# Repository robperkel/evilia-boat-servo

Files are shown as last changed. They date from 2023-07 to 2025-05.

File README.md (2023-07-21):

# Dr. Evilia's Boat Sampling HAT
This custom HAT is used to better implement control of the servos and motors used on her sampling boat. We found there wasn't a good "off-the-shelf" board available that fit the desired specifications. This project is designed around a small, 8-bit microcontroller that provides a far more intelligent and flexible design interface. 

This repository contains the documentation, hardware files, and firmware used for this project. The boat runs on a Raspberry Pi 4, Model B.  

## Table of Contents

- [Base Software](#base-software)
- [Tools Needed](#tools-needed)
    - [Other Tools Used](#other-tools-used)
- [Bill of Materials (BOM)](#bill-of-materials-bom)
- [Design Objectives](#design-objectives)
- [Microcontroller Pinout](#microcontroller-pinout)
- [Software Registers](#software-registers)
- [Digital Control](#digital-control)
- [Analog Control](#analog-control)
- [Usage from Raspberry Pi](#usage-from-raspberry-pi)

## Base Software

This bare metal I<sup>2</sup>C driver was used as a code base: https://github.com/microchip-pic-avr-examples/pic18f56q71-bare-metal-i2c-mplab 

**Per the license agreement in this code, the firmware (specifically the I<sup>2</sup>C driver) can ONLY be used with Microchip microcontrollers.** This is not an issue as the physical board is not compatiable with other microcontrollers.

## Tools Needed

- Programming / Development IDE: [MPLAB&reg; X IDE v6.10](https://www.microchip.com/en-us/tools-resources/develop/mplab-x-ide)
- Compiler: [MPLAB XC8 v2.41](https://www.microchip.com/en-us/tools-resources/develop/mplab-xc-compilers/downloads-documentation#XC8)  
- Programmer: [MPLAB SNAP](https://www.microchip.com/en-us/development-tool/PG164100) or [PICKIT&trade; 4](https://www.microchip.com/en-us/development-tool/PG164140)

### Other Tools Used

- I<sup>2</sup>C Tester (for development): [MCP2221A Breakout Module (ADM00559)](https://www.microchip.com/en-us/development-tool/ADM00559)
- Block Diagrams: [Draw.io](https://app.diagrams.net/)
- Schematic and PCB Generation: [KiCad 7](https://www.kicad.org/)
- PCB Vendor: [OSH Park](https://oshpark.com/)
    - If ordering from a different vendor, I recommend choosing a surface finish such as ENIG to provide some corrosion resistance in the high humidity environment.
    - Conformally coating the board is also recommended.

## Bill of Materials (BOM)

Order PCBs directly from the [OSH Park Project Page](https://oshpark.com/shared_projects/IClJSFr6)  
Digikey Shopping List: [https://www.digikey.com/en/mylists/list/YOLHZE0EBO](https://www.digikey.com/en/mylists/list/YOLHZE0EBO)   
- See [Control Board.xlsx](./Control%20Board/Control%20Board.xlsx) for the BOM
    - Red, struck-through items are not in the BOM
- Includes 0 ohm jumpers for I<sup>2</sup>C Address Setting
- Motor drive parts for `EXT_LED1` are not included
- Optional off-board connectors are not in the list

**Important: Shopping list does NOT include a programmer. Programmers can obtained from Digikey (or other electronics vendor).**

## Design Objectives

1. Support 6x 3-pin servo motors
2. ON/OFF control of a large pump
3. LED outputs for various indicators
4. I<sup>2</sup>C Interface
5. 3.3V logic interface with Raspberry Pi
6. 5V, 500mA motor control (ON/OFF)
7. 50 Hz Servo Frequency

## Microcontroller Pinout

Microcontroller: PIC18F1xQ41
(PIC18F14Q41 / PIC18F15Q41 / PIC18F16Q41)

| Function | Pin (PORT / PIN)
| --- | ---
| VDD (5V) | 1
| VSS (GND) | 20
| nMCLR | 4
| SDA | 2 (RA5)
| SCL | 3 (RA4)
| ADDR0 | 16 (RC0)
| ADDR1 | 13 (RB4)
| Servo 6 | 10 (RB7)
| Servo 5 | 9 (RC7)
| Servo 4 | 8 (RC6)
| Servo 3 | 7 (RC3)
| Servo 2 | 6 (RC4)
| Servo 1 | 5 (RC5)
| EXT_LED | 11 (RB6)
| PUMP_EN | 15 (RC1)
| AN1 | 17 (RA2)
| AN2 | 12 (RB5)
| DEBUG 0 | 19 (RA0 / ICSPDAT)
| DEBUG 1 | 18 (RA1 / ICSPCLK)
| OPAMP_OUT (reserved) | 14 (RC2)

### Notes
1. nMCLR is not available as an I/O in this configuration.
2. DEBUG 0/1 are LED outputs on the board. Unavailable during debugging.
3. EXT_LED can be converted to a 2nd motor/pump enable.
4. OPAMP_OUT is reserved due to internal OPAMP peripheral requirements.  

## Software Registers

**Please see [Registers.md](./Registers.md) for more information**

## Digital Control

### I<sup>2</sup>C Parameters

- Frequency: 100 kHz  
- 7-bit Address: TBD

### I<sup>2</sup>C Communication

### Writing To

The "register address" (Reg. ADDR) selects which setting to change. After this, each data byte is loaded into the next sequential register. 

(Start) &rarr; I<sup>2</sup>C ADDR (W) &rarr; Reg. ADDR &rarr; Data 0 &rarr; Data 1 &rarr; ... &rarr; Data N &rarr; (Stop)

### Reading From

To read from the device, address the microcontroller (write) and send the starting register address. Then, restart communication and address the microcontroller (read). Each byte is read in order from the registers.

(Start) &rarr; I<sup>2</sup>C ADDR (W) &rarr; Reg. ADDR &rarr; (Restart) &rarr; I<sup>2</sup>C ADDR (R) &rarr; Data 0 &rarr; Data 1 &rarr; ... &rarr; Data N &rarr; (Stop)

### Power on Restart (PoR) Behavior

On PoR, the microcontroller sets all duty cycles to 0%, PWM frequencies to 50 Hz, and turns off the LEDs and motor. 

## Analog Control

## Usage from Raspberry Pi

To ease integration in the system, a custom Python library was developed to simplify setup.

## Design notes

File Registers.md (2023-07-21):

# Software Registers

This file contains the software-defined registers, bitfields and allowed values.

## Register Map

| Address | Register Name | Description
| --- | --- | ---
| 0x00 | [STATUS](#status-register-mapping) | Status of the microcontroller
| 0x01 | [OUTPUT](#output-register-mapping) | Sets the output register (overwrites current value)
| 0x02 | [SAMPLE](#sample-register) | Selects the input to sample 
| 0x04 | [ADCH](#adchadcl-register) | ADC Measurement, High Byte
| 0x05 | [ADCL](#adchadcl-register) | ADC Measurement, Low Byte
| 0x06 | [PUMP_TIME](#pump_time-register) | Sets the on time of the PUMP_EN
| 0x07 | [LED_TIME](#led_time-register)  | Sets the on time of the EXT_LED
| 0x0A | [RESET](#reset-register) | Resets the microcontroller and returns  all settings to defaults
| 0x10 | [DC1H](#dcxhdcxl-registers) | Duty Cycle of PWM1, High Byte
| 0x11 | [DC1L](#dcxhdcxl-registers) | Duty Cycle of PWM1, Low Byte
| 0x12 | [DC2H](#dcxhdcxl-registers) | Duty Cycle of PWM2, High Byte
| 0x13 | [DC2L](#dcxhdcxl-registers) | Duty Cycle of PWM2, Low Byte
| 0x14 | [DC3H](#dcxhdcxl-registers) | Duty Cycle of PWM3, High Byte
| 0x15 | [DC3L](#dcxhdcxl-registers) | Duty Cycle of PWM3, Low Byte
| 0x16 | [DC4H](#dcxhdcxl-registers) | Duty Cycle of PWM4, High Byte
| 0x17 | [DC4L](#dcxhdcxl-registers) | Duty Cycle of PWM4, Low Byte
| 0x18 | [DC5H](#dcxhdcxl-registers) | Duty Cycle of PWM5, High Byte
| 0x19 | [DC5L](#dcxhdcxl-registers) | Duty Cycle of PWM5, Low Byte
| 0x1A | [DC6H](#dcxhdcxl-registers) | Duty Cycle of PWM6, High Byte
| 0x1B | [DC6L](#dcxhdcxl-registers) | Duty Cycle of PWM6, Low Byte
| 0x20 | [FRQ1H](#frqxhfrqxl-registers) | Frequency of PWM1/2, High Byte
| 0x21 | [FRQ1L](#frqxhfrqxl-registers) | Frequency of PWM1/2, Low Byte
| 0x22 | [FRQ2H](#frqxhfrqxl-registers) | Frequency of PWM3/4, High Byte
| 0x23 | [FRQ2L](#frqxhfrqxl-registers) | Frequency of PWM3/4, Low Byte
| 0x24 | [FRQ3H](#frqxhfrqxl-registers) | Frequency of PWM5/6, High Byte
| 0x25 | [FRQ3L](#frqxhfrqxl-registers) | Frequency of PWM5/6, Low Byte
| 0x30 | [Analog Configure](#analog-configure-register) | Configures the ADC for Analog Input 1
| 0x31 | [Gain Configure](#gain-configure-register) | Sets the OPAMP gain for Analog Input 1
| 0x32 | [DAC2 Output](#dac2-output-register)
| 0x50 | Firmware Update | Begins a firmware update operation
| 0x51 | Firmware Unlock 1 | See note 6
| 0x52 | Firmware Unlock 2 | See note 6
| 0x60 | Firmware Version ID | Firmware version identifier

### Notes

1. Each PWM is used to control each servo. 
2. PWM frequency and duty cycle is only updated on the low byte.
3. See "OUTPUT Register Mapping" for bitmapping of this byte.
4. Certain registers are kept at different offsets to reduce the chance of accidently modifying these values. 
5. PWM frequency is shared between paired outputs.
6. `Firmware Unlock 1` and `Firmware Unlock 2` are only accessible from a sequential write on `Firmware Update`. Other access attempts will be rejected.

**Note: Firmware update and version ID are currently not implemented.**

### STATUS Register Mapping

| Bit Position(s) | Function 
| --- | ---
| 7 | Pump State
| 6:3 | X
| 2 | EXT_LED State
| 1 | Error
| 0 | Sample Ready

### Notes
1. Sample Ready is cleared automatically when any part of the ADC value is read.  
2. The Error bit is set when an illegal command or operation occurs; Automatically cleared on read.
3. Pump/EXT_LED/PUMP_EN are clones of the `OUTPUT` register values.

### OUTPUT Register Mapping

| Bit Position(s) | Function 
| --- | ---
| 7 | Pump
| 6:3 | X
| 2 | External LED
| 1 | Debug LED1
| 0 | Debug LED0

Note: "X" values are reserved.

### SAMPLE Register

| Value | Sampled Input 
| ----- | ---
| 0x00  | *Unused*
| 0x01  | Analog Input 1
| 0x02  | Analog Input 2
| 0x03  | VSS (Ground)
| 0x04  | DAC2

### ADCH/ADCL Register

This value (up-to 16-bits) is the last conversion result from the ADC. Natively, the ADC is 12 bits. But, oversampling can be used for more resolution.

The ADCH value is the high byte, while the ADCL value is the low byte.

### PUMP_TIME Register

| Bit Position(s) | Function 
| --- | ---
| 7:0 | Maximum time (in seconds) for the pump to be on for

* If `PUMP_TIME` is set to 0, then there is no timeout for the pump. 
* Initializes to 120s on Power on Reset (PoR).

### LED_TIME Register

| Bit Position(s) | Function 
| --- | ---
| 7:0 | Maximum time (in seconds) for the external LED to be on for

* If `LED_TIME` is set to 0, then there is no timeout for the LED. 
* Initializes to 0 (disabled) on Power on Reset (PoR).  

### RESET Register

| Value | Function 
| ----- | ---
| 0x5A  | RESET the microcontroller

Note: All other values loaded into this register are ignored.

### DCxH/DCxL Registers

This register holds the 16-bit value used by the PWM hardware to set the duty cycle. The DCxH value is the high byte, while the DCxL value is the low byte.

### FRQxH/FRQxL Registers

This register holds the 16-bit value used by the PWM hardware to set the period (frequency) of the waveform. The FRQxH value is the high byte, while the FRQxL value is the low byte.

### Analog Configure Register

| Bit Position | Function 
| --- | ---
| 7:6 | Voltage Reference Select
| 5:4 | X
| 3:0 | Averaging Configuration

#### Bit Description

Voltage Reference Select
- 0b00 = VDD (5V)
- 0b01 = FVR 1.024V
- 0b10 = FVR 2.048V
- 0b11 = FVR 4.096V

FVR - Fixed Voltage Reference; Internal to the microcontroller. See datasheet for performance, accuracy, etc...

Averaging Configuration
- 0b0000 = 1 Sample (No Averaging)
- 0b0001 = 2 Samples
- 0b0010 = 4 Samples
- 0b0011 = 8 Samples
- 0b0100 = 16 Samples

Note: Undefined values will be treated as 0b0000 (1 sample).

### Gain Configure Register

| Bit Position | Function 
| --- | ---
| 7:3 | X
| 3:0 | Gain Configuration

Note: "X" values are reserved.

#### Bit Description

Gain Configuration
- 0b1xxx = 1 (Unity Gain)
- 0b0000 = 16/15
- 0b0001 = 8/7
- 0b0010 = 4/3
- 0b0011 = 2
- 0b0100 = 8/3
- 0b0101 = 4
- 0b0110 = 8
- 0b0111 = 16

For gain changes, some time is required for the output to stabilize. But, I<sup>2</sup>C is relatively slow, so there shouldn't be any timing issues with starting a conversion immediately following a gain change (assuming 100 kHz speed). 

### DAC2 Output Register

Sets the output voltage of DAC2. DAC2 uses the 1.024V FVR. The output is set by the formula: Vout = DATA/2^8 * 1.024V

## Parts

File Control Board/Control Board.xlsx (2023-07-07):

Date: | 2023-07-05 12:13
Tool: | Eeschema 7.0.5
Generator: | C:\Program Files\KiCad\7.0\bin\scripting\plugins/bom_csv_grouped_by_value_with_fp.py
Component Count: | 72
Ref | Qnty | Value | Cmp name | Footprint | Description | Vendor | DNP
ADDR0, ADDR1 | 2 | 0 | R_US | Resistor_SMD:R_0805_2012Metric_Pad1.20x1.40mm_HandSolder | Resistor, US symbol |  | DNP
~~ANALOG_EXT1, ANALOG_EXT2~~ | ~~2~~ | ~~Conn_01x03_Pin~~ | ~~Conn_01x03_Pin~~ | ~~Connector_PinHeader_2.54mm:PinHeader_1x03_P2.54mm_Vertical~~ | ~~Generic connector, single row, 01x03, script generated~~ |  | DNP
BAT_IN1 | 1 | BCH-381H-2GN | Terminal_Block_2 | Control Board Custom:BCH-381H-2GN | Terminal Block
~~C1, C3, C5, C7, C8, C9, C10, C11, C12, C13, C14~~ | ~~11~~ | ~~0.01uF~~ | ~~C_Small~~ | ~~Capacitor_SMD:C_0805_2012Metric_Pad1.18x1.45mm_HandSolder~~ | ~~Unpolarized capacitor, small symbol~~ |  | ~~DNP~~
C15 | 1 | 220uF | C_Polarized | Capacitor_THT:C_Radial_D8.0mm_H11.5mm_P3.50mm | Polarized capacitor
C2, C4, C6 | 3 | 0.1uF | C_Small | Capacitor_SMD:C_0805_2012Metric_Pad1.18x1.45mm_HandSolder | Unpolarized capacitor, small symbol
D1 | 1 | MBR0580S1 | MBR0580S1_1 | StandardPackages_Custom:SOD-123 | 0.5A, SMD Schottky Diode
~~D2~~ | ~~1~~ | ~~MBR0580S1~~ | ~~MBR0580S1_1~~ | ~~StandardPackages_Custom:SOD-123~~ | ~~0.5A, SMD Schottky Diode~~ |  | ~~DNP~~
D3, D4 | 2 | SMAJ6.0A | SMAJ | StandardPackages_Custom:DO-214AC | SMAJ Series TVS (Zener Type) by Littelfuse
D5 | 1 | B240AE-13 | Schottky Diode | StandardPackages_Custom:DO-214AC | Schottky Diode, Generic Symbol
D6, D7, D8 | 3 | LED_Small_Filled | LED_Small_Filled | LED_SMD:LED_0805_2012Metric_Pad1.15x1.40mm_HandSolder | Light emitting diode, small symbol, filled shape
~~EXT_I2C1, EXT_I2C2~~ | ~~2~~ | ~~Conn_01x04_Pin~~ | ~~Conn_01x04_Pin~~ | ~~Connector_PinHeader_2.54mm:PinHeader_1x04_P2.54mm_Vertical~~ | ~~Generic connector, single row, 01x04, script generated~~ |  | ~~DNP~~
EXT_LED1 | 1 | BCH-381H-2 GN | Terminal_Block | Control Board Custom:BCH-381H-2GN | Terminal Block
<Terminal Block Plugs for BAT_IN1, EXT_LED1, PUMP_IN1> | 3 | BCP-381- 2 GN | Terminal Block Header
J1 | 1 | Raspberry_Pi_2_3 | Raspberry_Pi_2_3 | Connector_PinHeader_2.54mm:PinHeader_2x20_P2.54mm_Vertical | expansion header for Raspberry Pi 2 & 3
PICKIT1 | 1 | Conn_01x06 | Conn_01x06 | Connector_PinHeader_2.54mm:PinHeader_1x06_P2.54mm_Horizontal | Generic connector, single row, 01x06, script generated (kicad-library-utils/schlib/autogen/connector/)
PTC2 | 1 | 1.1A | PTC_1 | Control Board Custom:0ZCG Series PTC | PTC, Self-Resetting Thermal Fuses
PTC3 | 1 | 100mA | PTC_1 | Control Board Custom:0ZCG Series PTC | PTC, Self-Resetting Thermal Fuses
PUMP_IN1 | 1 | BCH-381H-2GN | Terminal_Block_1 | Control Board Custom:BCH-381H-2GN | Terminal Block
Q1, Q2 | 2 | BSS214NH | BSS214NH_1 | StandardPackages_Custom:SOT23-3 | BSS214NH, SOT-23-3 MOSFET by Infineon
R1, R7, R8, R9 | 4 | 10k | R_US | Resistor_SMD:R_0805_2012Metric_Pad1.20x1.40mm_HandSolder | Resistor, US symbol
R12, R21 | 2 | 100 | R_US | Resistor_SMD:R_0805_2012Metric_Pad1.20x1.40mm_HandSolder | Resistor, US symbol
R13, R22 | 2 | 100k | R_US | Resistor_SMD:R_0805_2012Metric_Pad1.20x1.40mm_HandSolder | Resistor, US symbol
R2, R14, R15, R16, R17, R18, R19, R20, R25 | 9 | 470 | R_US | Resistor_SMD:R_0805_2012Metric_Pad1.20x1.40mm_HandSolder | Resistor, US symbol
~~R23~~ | ~~1~~ | ~~0~~ | ~~R_US~~ | ~~Resistor_SMD:R_0805_2012Metric_Pad1.20x1.40mm_HandSolder~~ | ~~Resistor, US symbol~~ |  | ~~DNP~~
R24 | 1 | 1k | R_US | Resistor_SMD:R_0805_2012Metric_Pad1.20x1.40mm_HandSolder | Resistor, US symbol
~~R3, R4, R10, R11~~ | ~~4~~ | ~~10k~~ | ~~R_US~~ | ~~Resistor_SMD:R_0805_2012Metric_Pad1.20x1.40mm_HandSolder~~ | ~~Resistor, US symbol~~ |  | ~~DNP~~
RST_SW1 | 1 | TL6400AF160QJ | SW_Push | Control Board Custom:TL6400AF160QJ | Push button switch, generic, two pins
SERVO1, SERVO2, SERVO3, SERVO4, SERVO5, SERVO6 | 6 | Conn_01x03_Pin | Conn_01x03_Pin | Connector_PinHeader_2.54mm:PinHeader_1x03_P2.54mm_Vertical | Generic connector, single row, 01x03, script generated
~~STEMMA1~~ | ~~1~~ | ~~JST SH~~ | ~~STEMMA_4-pin_I2C~~ | ~~Connector_Adafruit_Custom:Adafruit STEMMA, 4-pin JST SH~~ | ~~4-pin Stemma connector for I2C. ~~ |  | ~~DNP~~
~~STEMMA4~~ | ~~1~~ | ~~JST PH~~ | ~~STEMMA_3-pin_Analog/Digital/PWM~~ | ~~Connector_Adafruit_Custom:Adafruit STEMMA, 3-pin JST PH~~ | ~~3-Pin STEMMA connector analog, digital, or PWM signals~~ |  | ~~DNP~~
U1 | 1 | PIC18F16Q41 | PIC18F1xQ40/41 | StandardPackages_Custom:SSOP-20, 5.3mm Body | PIC18-Q40/Q41 Family of Microcontrollers, 20-pin
U2 | 1 | PI4ULS5V202UEX | PI4ULS5V202 | StandardPackages_Custom:MSOP-8 | Auto Direction Sensing 2-bit Level Shifter by Pericom (Diodes Inc.)

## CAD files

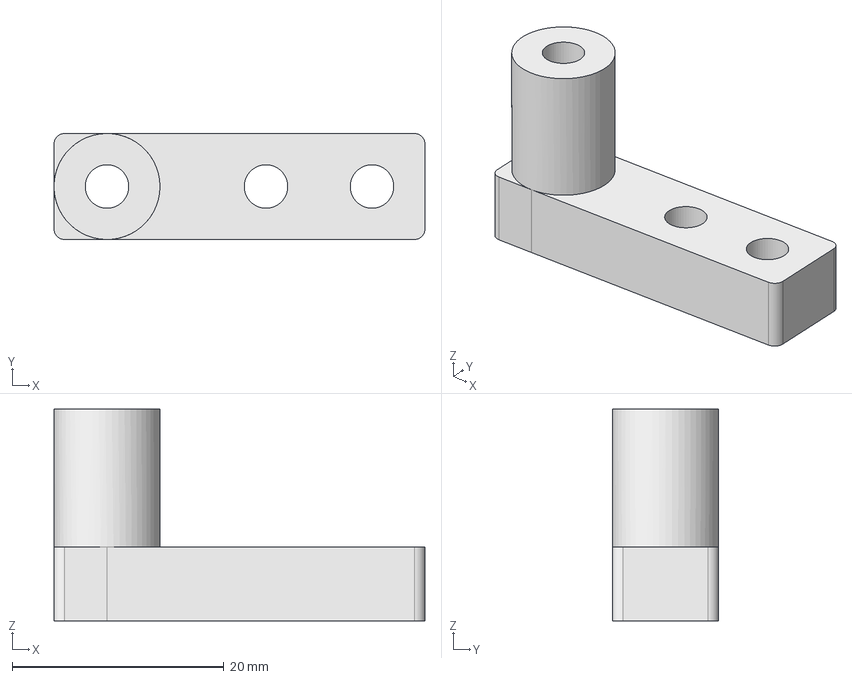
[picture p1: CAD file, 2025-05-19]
3D Models/flagMount.FCStd
35.0 x 10.0 x 20.0 mm

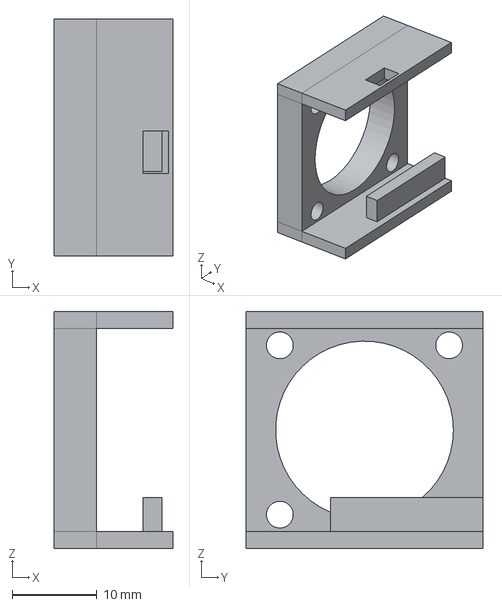
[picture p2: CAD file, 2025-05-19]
3D Models/cameraBox.step
14.0 x 28.0 x 28.0 mm

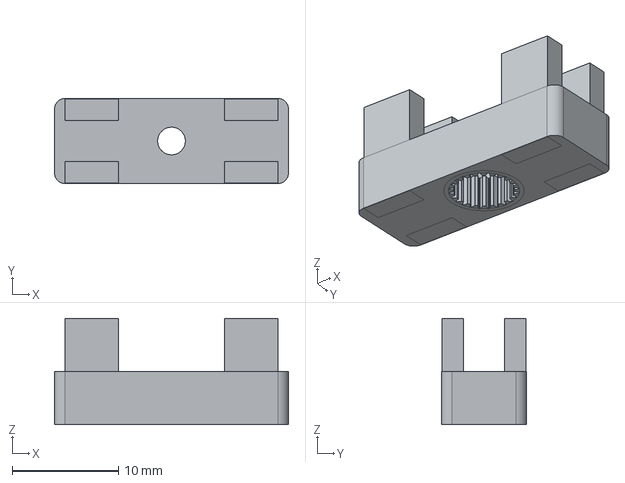
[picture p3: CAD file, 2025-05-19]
3D Models/valve interface v3.step
22.0 x 8.00 x 10.0 mm

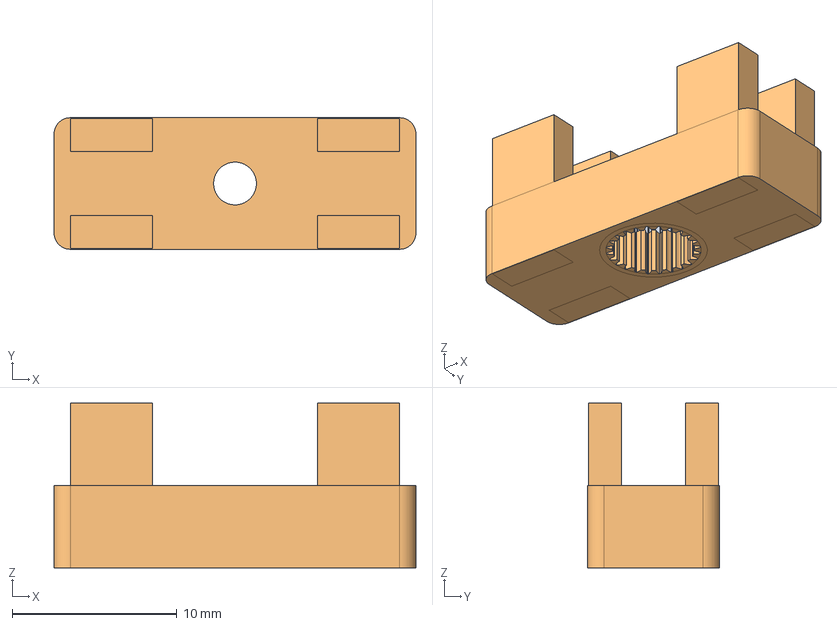
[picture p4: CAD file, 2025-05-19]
3D Models/valve interface.FCStd
22.0 x 8.00 x 10.0 mm

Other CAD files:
3D Models/cameraBox.FCStd

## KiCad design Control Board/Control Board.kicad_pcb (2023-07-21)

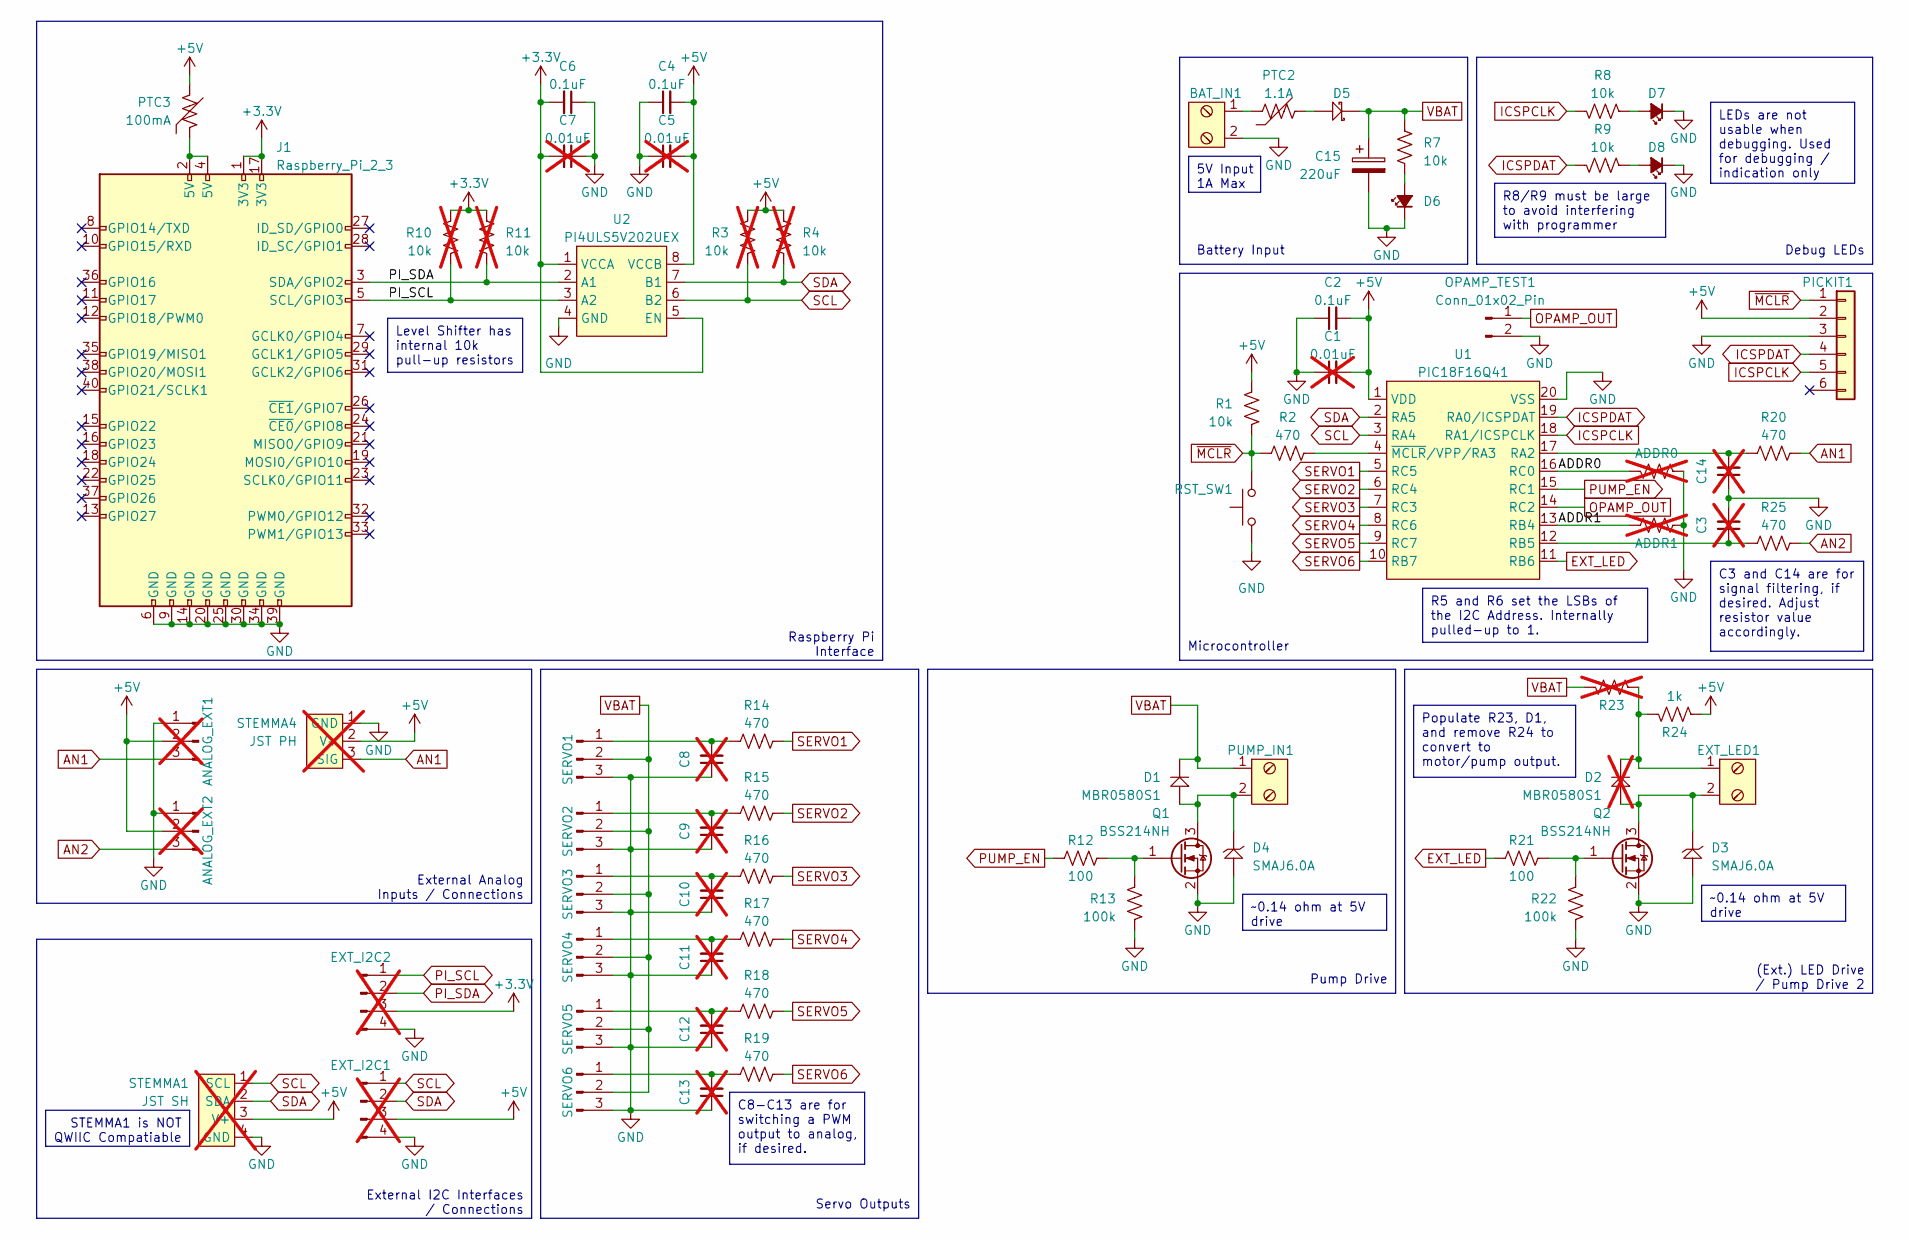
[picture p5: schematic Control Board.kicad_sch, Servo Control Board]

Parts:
ADDR0, ADDR1: 0; R_0805_2012Metric_Pad1.20x1.40mm_HandSolder; not fitted
ANALOG_EXT1, ANALOG_EXT2: Conn_01x03_Pin; PinHeader_1x03_P2.54mm_Vertical; not fitted
BAT_IN1: BCH-381H-2 GN; BCH-381H-2GN
C1, C3, C5, C7, C8, C9, C10, C11, C12, C13, C14: 0.01uF; C_0805_2012Metric_Pad1.18x1.45mm_HandSolder; not fitted
C2, C4, C6: 0.1uF; C_0805_2012Metric_Pad1.18x1.45mm_HandSolder
C15: 220uF; C_Radial_D8.0mm_H11.5mm_P3.50mm
D1: MBR0580S1; SOD-123
D2: MBR0580S1; SOD-123; not fitted
D3, D4: SMAJ6.0A; DO-214AC
D5: B240AE-13; DO-214AC
D6, D7, D8: LED_Small_Filled; LED_0805_2012Metric_Pad1.15x1.40mm_HandSolder
EXT_I2C1, EXT_I2C2: Conn_01x04_Pin; PinHeader_1x04_P2.54mm_Vertical; not fitted
EXT_LED1: BCH-381H-2 GN; BCH-381H-2GN
J1: Raspberry_Pi_2_3; PinHeader_2x20_P2.54mm_Vertical
OPAMP_TEST1: Conn_01x02_Pin; PinHeader_1x02_P2.54mm_Vertical
PICKIT1: Conn_01x06; PinHeader_1x06_P2.54mm_Horizontal
PTC2: 1.1A; 0ZCG Series PTC
PTC3: 100mA; 0ZCG Series PTC
PUMP_IN1: BCH-381H-2 GN; BCH-381H-2GN
Q1, Q2: BSS214NH; SOT23-3
R1, R7, R8, R9: 10k; R_0805_2012Metric_Pad1.20x1.40mm_HandSolder
R2, R14, R15, R16, R17, R18, R19, R20, R25: 470; R_0805_2012Metric_Pad1.20x1.40mm_HandSolder
R3, R4, R10, R11: 10k; R_0805_2012Metric_Pad1.20x1.40mm_HandSolder; not fitted
R12, R21: 100; R_0805_2012Metric_Pad1.20x1.40mm_HandSolder
R13, R22: 100k; R_0805_2012Metric_Pad1.20x1.40mm_HandSolder
R23: 0; R_0805_2012Metric_Pad1.20x1.40mm_HandSolder; not fitted
R24: 1k; R_0805_2012Metric_Pad1.20x1.40mm_HandSolder
RST_SW1: TL6400AF160QJ
SERVO1, SERVO2, SERVO3, SERVO4, SERVO5, SERVO6: Conn_01x03_Pin; PinHeader_1x03_P2.54mm_Vertical
STEMMA1: JST SH; Adafruit STEMMA, 4-pin JST SH; not fitted
STEMMA4: JST PH; Adafruit STEMMA, 3-pin JST PH; not fitted
U1: PIC18F16Q41; SSOP-20, 5.3mm Body
U2: PI4ULS5V202UEX; MSOP-8

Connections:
+3.3V: C6.2, C7.2, EXT_I2C2.3, J1.1 (3V3), J1.17 (3V3), R10.1, R11.1, U2.1 (VCCA), U2.5 (EN)
+5V: ANALOG_EXT1.2, ANALOG_EXT2.2, C1.2, C2.2, C4.2, C5.2, EXT_I2C1.3, PICKIT1.2, PTC3.2, R1.1, R3.1, R4.1, R24.2, STEMMA1.3 (V+), STEMMA4.2 (V+), U1.1 (VDD), U2.8 (VCCB)
/ADDR0: ADDR0.1, U1.16 (RC0)
/ADDR1: ADDR1.1, U1.13 (RB4)
AN1: ANALOG_EXT1.3, R20.2, STEMMA4.3 (SIG)
AN2: ANALOG_EXT2.3, R25.2
EXT_LED: R21.1, U1.11 (RB6)
GND: ADDR0.2, ADDR1.2, ANALOG_EXT1.1, ANALOG_EXT2.1, BAT_IN1.2, C1.1, C2.1, C3.2, C4.1, C5.1, C6.1, C7.1, C8.1, C9.1, C10.1, C11.1, C12.1, C13.1, C14.1, C15.2, D3.A, D4.A, D6.1 (K), D7.1 (K), D8.1 (K), EXT_I2C1.4, EXT_I2C2.4, J1.6 (GND), J1.9 (GND), J1.14 (GND), J1.20 (GND), J1.25 (GND), J1.30 (GND), J1.34 (GND), J1.39 (GND), OPAMP_TEST1.2, PICKIT1.3, Q1.2 (S), Q2.2 (S), R13.2, R22.2, RST_SW1.1, SERVO1.3, SERVO2.3, SERVO3.3, SERVO4.3, SERVO5.3, SERVO6.3, STEMMA1.4 (GND), STEMMA4.1 (GND), U1.20 (VSS), U2.4 (GND)
ICSPCLK: PICKIT1.5, R8.2, U1.18 (RA1/ICSPCLK)
ICSPDAT: PICKIT1.4, R9.2, U1.19 (RA0/ICSPDAT)
unnamed: BAT_IN1.1, PTC2.1
unnamed: D2.K, EXT_LED1.1, R23.2, R24.1
unnamed: D5.A, PTC2.2
unnamed: D6.2 (A), R7.2
unnamed: D7.2 (A), R8.1
unnamed: D8.2 (A), R9.1
unnamed: J1.2 (5V), J1.4 (5V), PTC3.1
unnamed: D1.A, D4.K, PUMP_IN1.2, Q1.3 (D)
unnamed: Q1.1 (G), R12.2, R13.1
unnamed: D2.A, D3.K, EXT_LED1.2, Q2.3 (D)
unnamed: Q2.1 (G), R21.2, R22.1
unnamed: C8.2, R14.1, SERVO1.1
unnamed: C9.2, R15.1, SERVO2.1
unnamed: C10.2, R16.1, SERVO3.1
unnamed: C11.2, R17.1, SERVO4.1
unnamed: C12.2, R18.1, SERVO5.1
unnamed: C13.2, R19.1, SERVO6.1
unnamed: C14.2, R20.1, U1.17 (RA2)
unnamed: C3.1, R25.1, U1.12 (RB5)
unnamed: R2.2, U1.4 (~MCLR/VPP/RA3)
OPAMP_OUT: OPAMP_TEST1.1, U1.14 (RC2)
PI_SCL: EXT_I2C2.1, J1.5 (SCL/GPIO3), R10.2, U2.3 (A2)
PI_SDA: EXT_I2C2.2, J1.3 (SDA/GPIO2), R11.2, U2.2 (A1)
PUMP_EN: R12.1, U1.15 (RC1)
SCL: EXT_I2C1.1, R3.2, STEMMA1.1 (SCL), U1.3 (RA4), U2.6 (B2)
SDA: EXT_I2C1.2, R4.2, STEMMA1.2 (SDA), U1.2 (RA5), U2.7 (B1)
SERVO1: R14.2, U1.5 (RC5)
SERVO2: R15.2, U1.6 (RC4)
SERVO3: R16.2, U1.7 (RC3)
SERVO4: R17.2, U1.8 (RC6)
SERVO5: R18.2, U1.9 (RC7)
SERVO6: R19.2, U1.10 (RB7)
VBAT: C15.1, D1.K, D5.K, PUMP_IN1.1, R7.1, R23.1, SERVO1.2, SERVO2.2, SERVO3.2, SERVO4.2, SERVO5.2, SERVO6.2
~MCLR: PICKIT1.1, R1.2, R2.1, RST_SW1.2

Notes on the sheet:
Populate R23, D1, and remove R24 to convert to motor/pump output.
Debug LEDs
External Analog Inputs / Connections
Battery Input
~0.14 ohm at 5V drive
R8/R9 must be large to avoid interfering with programmer
5V Input 1A Max
C3 and C14 are for signal filtering, if desired. Adjust resistor value accordingly.
C8-C13 are for switching a PWM output to analog, if desired.
External I2C Interfaces / Connections
LEDs are not usable when debugging. Used for debugging / indication only
Pump Drive
Level Shifter has internal 10k pull-up resistors
R5 and R6 set the LSBs of the I2C Address. Internally pulled-up to 1.
Servo Outputs
Microcontroller
(Ext.) LED Drive / Pump Drive 2
STEMMA1 is NOT QWIIC Compatiable
Raspberry Pi Interface

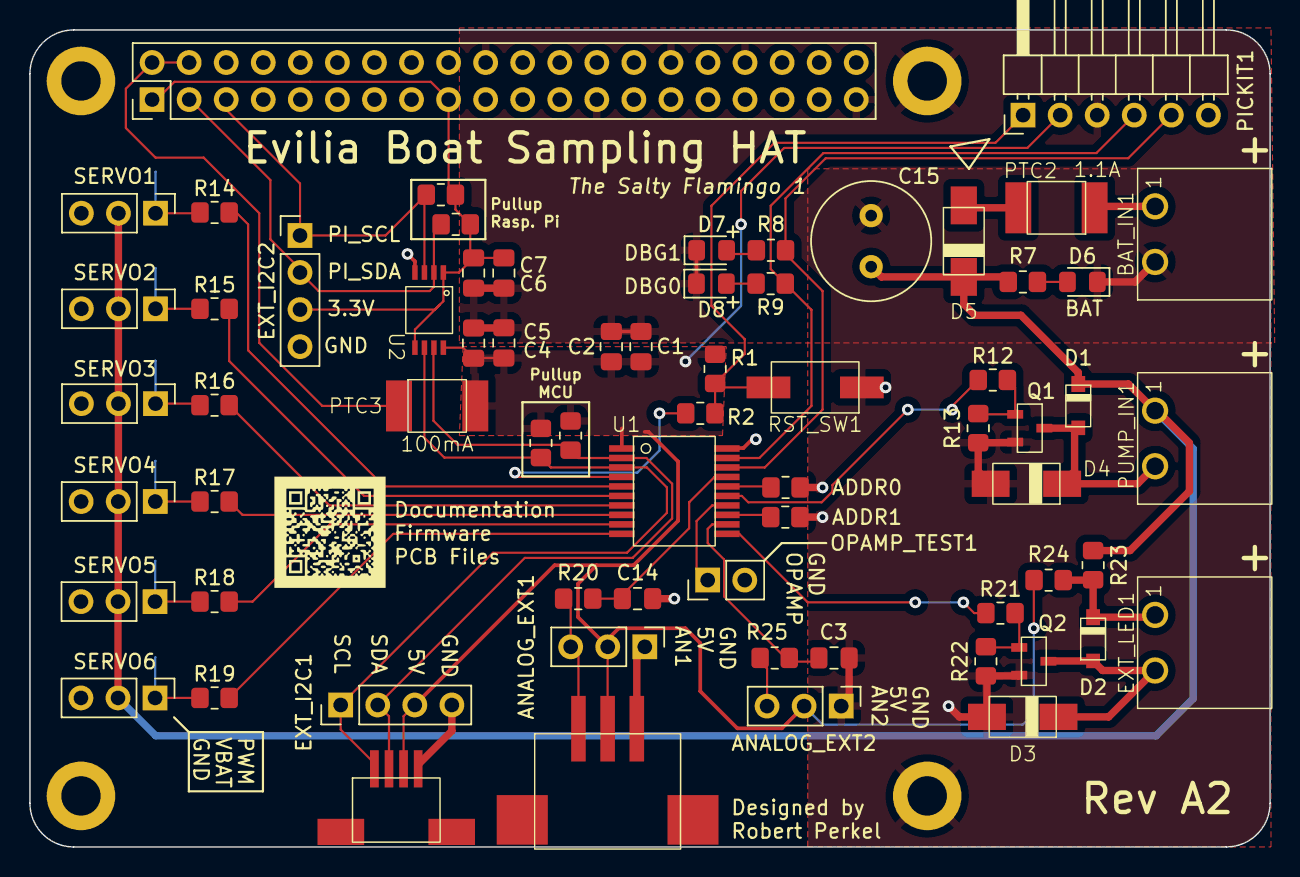
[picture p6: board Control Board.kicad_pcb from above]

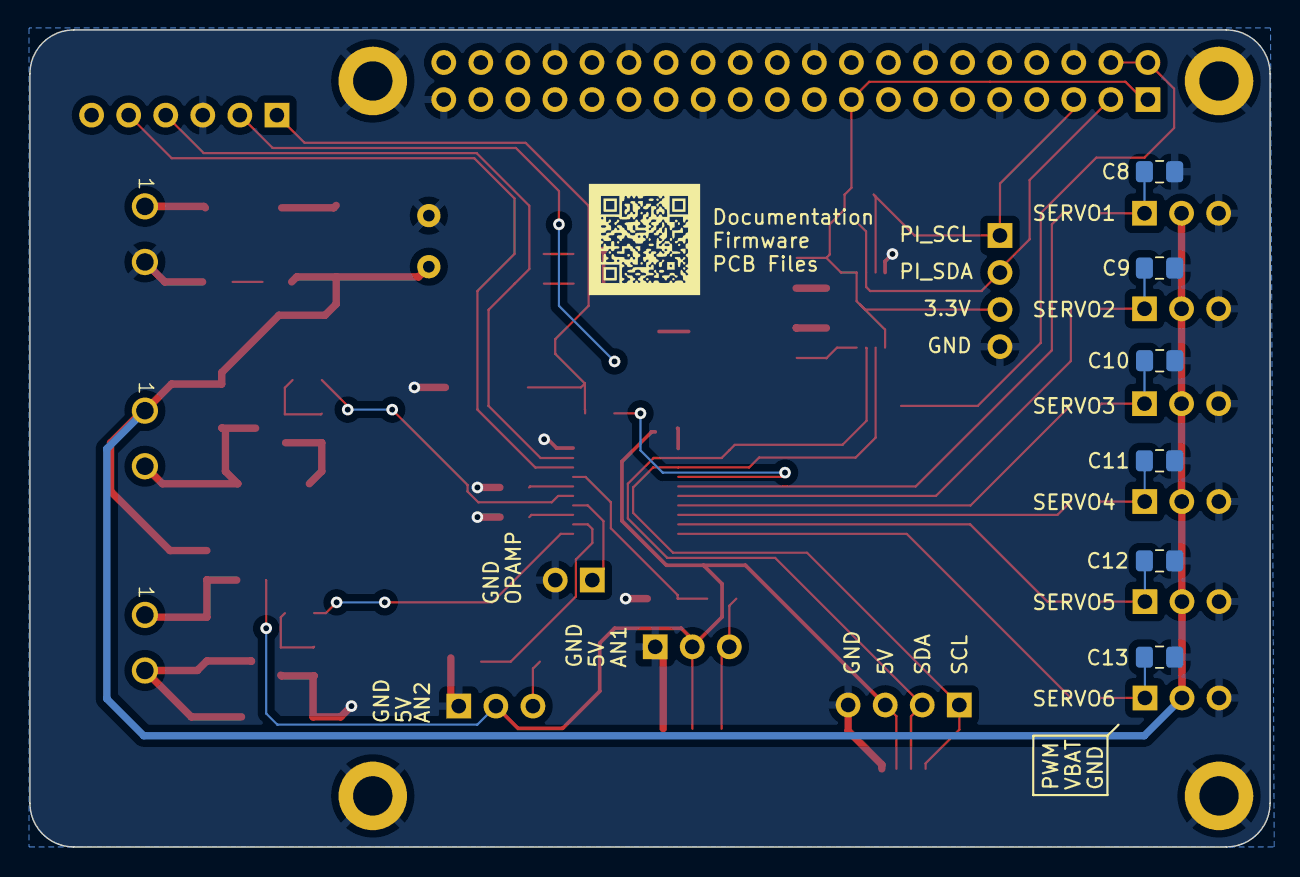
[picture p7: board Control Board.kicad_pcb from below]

Board: 2 copper layers, 85.0 x 56.0 mm, 73 parts (6 on the bottom side), 44 nets.

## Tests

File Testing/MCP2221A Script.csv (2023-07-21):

True | I2C | 7 bit | 0x43 | Write | 0x00 | Select STATUS | Send
True | I2C | 7 bit | 0x43 | Read | 1 | Read STATUS | Send
True | I2C | 7 bit | 0x43 | Write | 0x02, 0x04 | Select SAMPLE | Send
True | I2C | 7 bit | 0x43 | Write | 0x00 | Select STATUS | Send
True | I2C | 7 bit | 0x43 | Read | 1 | Read STATUS | Send
True | I2C | 7 bit | 0x43 | Write | 0x04 | Select ADCH | Send
True | I2C | 7 bit | 0x43 | Read | 2 | Read Result | Send
True | I2C | 7 bit | 0x43 | Write | 0x10, 0x03, 0xE8 | SERVO1 PW 2ms | Send
True | I2C | 7 bit | 0x43 | Write | 0x12, 0x02, 0xEE | SERVO2 PW 1.5ms | Send
True | I2C | 7 bit | 0x43 | Write | 0x14, 0x03, 0xE8 | SERVO3 PW 2ms | Send
True | I2C | 7 bit | 0x43 | Write | 0x16, 0x02, 0xEE | SERVO4 PW 1.5ms | Send
True | I2C | 7 bit | 0x43 | Write | 0x18, 0x03, 0xE8 | SERVO5 PW 2ms | Send
True | I2C | 7 bit | 0x43 | Write | 0x1A, 0x02, 0xEE | SERVO6 PW 1.5ms | Send
True | I2C | 7 bit | 0x43 | Write | 0x10 | Select SERVO1 PW | Send
True | I2C | 7 bit | 0x43 | Read | 12 | Read all Servo Parameters | Send
True | I2C | 7 bit | 0x43 | Write | 0x20, 0x13, 0x88 | SERVO1 FRQ 100 Hz | Send
True | I2C | 7 bit | 0x43 | Write | 0x22, 0x09, 0xC4 | SERVO2 FRQ 200 Hz | Send
True | I2C | 7 bit | 0x43 | Write | 0x24, 0x13, 0x88 | SERVO3 FRQ 100 Hz | Send
True | I2C | 7 bit | 0x43 | Write | 0x20 | Select SERVO1 FRQ | Send
True | I2C | 7 bit | 0x43 | Read | 6 | READ SERVOx FRQ | Send
True | I2C | 7 bit | 0x43 | Write | 0x32, 0x20 |  | Send

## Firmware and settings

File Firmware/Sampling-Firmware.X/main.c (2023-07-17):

// PIC18F16Q41 Configuration Bit Settings

// 'C' source line config statements

// CONFIG1
#pragma config FEXTOSC = OFF    // External Oscillator Selection (Oscillator not enabled)
#pragma config RSTOSC = HFINTOSC_64MHZ// Reset Oscillator Selection (HFINTOSC with HFFRQ = 64 MHz and CDIV = 1:1)

// CONFIG2
#pragma config CLKOUTEN = OFF   // Clock out Enable bit (CLKOUT function is disabled)
#pragma config PR1WAY = OFF     // PRLOCKED One-Way Set Enable bit (PRLOCKED bit can be set and cleared repeatedly)
#pragma config CSWEN = ON       // Clock Switch Enable bit (Writing to NOSC and NDIV is allowed)
#pragma config FCMEN = ON       // Fail-Safe Clock Monitor Enable bit (Fail-Safe Clock Monitor enabled)
#pragma config FCMENP = ON      // Fail-Safe Clock Monitor - Primary XTAL Enable bit (Fail-Safe Clock Monitor enabled; timer will flag FSCMP bit and OSFIF interrupt on EXTOSC failure.)
#pragma config FCMENS = ON      // Fail-Safe Clock Monitor - Secondary XTAL Enable bit (Fail-Safe Clock Monitor enabled; timer will flag FSCMP bit and OSFIF interrupt on SOSC failure.)

// CONFIG3
#pragma config MCLRE = EXTMCLR  // MCLR Enable bit (If LVP = 0, MCLR pin is MCLR; If LVP = 1, RE3 pin function is MCLR )
#pragma config PWRTS = PWRT_OFF // Power-up timer selection bits (PWRT is disabled)
#pragma config MVECEN = ON      // Multi-vector enable bit (Multi-vector enabled, Vector table used for interrupts)
#pragma config IVT1WAY = ON     // IVTLOCK bit One-way set enable bit (IVTLOCKED bit can be cleared and set only once)
#pragma config LPBOREN = OFF    // Low Power BOR Enable bit (Low-Power BOR disabled)
#pragma config BOREN = SBORDIS  // Brown-out Reset Enable bits (Brown-out Reset enabled , SBOREN bit is ignored)

// CONFIG4
#pragma config BORV = VBOR_2P85 // Brown-out Reset Voltage Selection bits (Brown-out Reset Voltage (VBOR) set to 2.8V)
#pragma config ZCD = OFF        // ZCD Disable bit (ZCD module is disabled. ZCD can be enabled by setting the ZCDSEN bit of ZCDCON)
#pragma config PPS1WAY = OFF    // PPSLOCK bit One-Way Set Enable bit (PPSLOCKED bit can be set and cleared repeatedly (subject to the unlock sequence))
#pragma config STVREN = ON      // Stack Full/Underflow Reset Enable bit (Stack full/underflow will cause Reset)
#pragma config LVP = ON         // Low Voltage Programming Enable bit (Low voltage programming enabled. MCLR/VPP pin function is MCLR. MCLRE configuration bit is ignored)
#pragma config XINST = OFF      // Extended Instruction Set Enable bit (Extended Instruction Set and Indexed Addressing Mode disabled)

// CONFIG5
#pragma config WDTCPS = WDTCPS_11// WDT Period selection bits (Divider ratio 1:65536)
#pragma config WDTE = ON        // WDT operating mode (WDT enabled regardless of sleep; SWDTEN is ignored)

// CONFIG6
#pragma config WDTCWS = WDTCWS_6// WDT Window Select bits (window always open (100%); no software control; keyed access required)
#pragma config WDTCCS = LFINTOSC// WDT input clock selector (WDT reference clock is the 31.0 kHz LFINTOSC)

// CONFIG7
#pragma config BBSIZE = BBSIZE_512// Boot Block Size selection bits (Boot Block size is 512 words)
#pragma config BBEN = OFF       // Boot Block enable bit (Boot block disabled)
#pragma config SAFEN = OFF      // Storage Area Flash enable bit (SAF disabled)
#pragma config DEBUG = OFF      // Background Debugger (Background Debugger disabled)

// CONFIG8
#pragma config WRTB = OFF       // Boot Block Write Protection bit (Boot Block not Write protected)
#pragma config WRTC = OFF       // Configuration Register Write Protection bit (Configuration registers not Write protected)
#pragma config WRTD = OFF       // Data EEPROM Write Protection bit (Data EEPROM not Write protected)
#pragma config WRTSAF = OFF     // SAF Write protection bit (SAF not Write Protected)
#pragma config WRTAPP = OFF     // Application Block write protection bit (Application Block not write protected)

// CONFIG9
#pragma config CP = OFF         // PFM and Data EEPROM Code Protection bit (PFM and Data EEPROM code protection disabled)

// #pragma config statements should precede project file includes.
// Use project enums instead of #define for ON and OFF.

#include <xc.h>

#include "i2c_client.h"
#include "interrupts.h"
#include "GPIO.h"
#include "I2C_FSM.h"
#include "SW_Registers.h"
#include "system.h"
#include "self_test.h"
#include "GPIO_Macros.h"
#include "TMR2.h"

void main(void) {
    
    //Init Hardware Peripherals
    System_init();
    
    //Init I2C SW State Machine
    I2C_FSM_init();
    
    //Init SW Defined Registers
    Registers_init();

    //Assign I2C Interrupt Handlers
    I2C_assignByteWriteHandler(&I2C_FSM_handleWrite);
    I2C_assignByteReadHandler(&I2C_FSM_handleRead);
    I2C_assignStopHandler(&I2C_FSM_handleStop);
        
    //Enable Interrupts
    Interrupts_enable();
    
    //If the project is in HW_TEST configuration
    //The self-test will execute on PoR
#ifdef HW_SELF_TEST
    selfTest_runAll();
#endif
    
    //NOTE: WDT is set to 2s
    
    while (1)
    {
        //Does the WDT need to be cleared?
        if (System_getWDTFlag())
        {
            //Clear WDT
            System_clearWDT();
        }
    }
    
    return;
}

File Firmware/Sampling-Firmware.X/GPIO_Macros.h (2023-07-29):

#ifndef GPIO_MACROS_H
#define	GPIO_MACROS_H

#ifdef	__cplusplus
extern "C" {
#endif

#include <xc.h>
    
//Register Macros
    
//LAT - Latched Output Values
#define LAT_HIGH 1
#define LAT_LOW 0    
    
//TRIS - Tristate Control (I/O Direction)
#define TRIS_INPUT 1
#define TRIS_OUTPUT 0
    
//ANSEL - Analog Select
#define ANSEL_ANALOG 1
#define ANSEL_DIGITAL 0
    
//WPU - Weak Pull-Ups
#define WPU_ENABLED 1
#define WPU_DISABLED 0
    
//INLVL - Input Levels
#define INLVL_ST 1 //Schmitt Trigger Levels
#define INLVL_TTL 0 //TTL Logic Levels
    
//SLRCON - Slew Rate Limiters
#define SLRCON_LIMITED 1
#define SLRCON_NO_LIMIT 0
    
//ODCON - Open Drain Enable
#define ODCON_OPEN_DRAIN 1
#define ODCON_PUSH_PULL 0

//I/O Macros
    
//PUMP_EN Output - RC1
#define PUMP_EN_LAT LATC1
#define PUMP_EN_TRIS TRISC1
#define PUMP_EN_ANSEL ANSELC1
#define PUMP_EN_SetHigh() PUMP_EN_LAT = 1
#define PUMP_EN_SetLow() PUMP_EN_LAT = 0
#define PUMP_EN_GetValue() PUMP_EN_LAT
    
//EXT_LED Output - RB6
#define EXT_LED_LAT LATB6
#define EXT_LED_TRIS TRISB6
#define EXT_LED_ANSEL ANSELB6
#define EXT_LED_SetHigh() EXT_LED_LAT = 1
#define EXT_LED_SetLow() EXT_LED_LAT = 0
#define EXT_LED_GetValue() EXT_LED_LAT
    
//DEBUG1 Output - RA1
#define DEBUG1_LAT LATA1
#define DEBUG1_TRIS TRISA1
#define DEBUG1_ANSEL ANSELA1
#define DEBUG1_SetHigh() DEBUG1_LAT = 1
#define DEBUG1_SetLow() DEBUG1_LAT = 0
#define DEBUG1_Toggle() DEBUG1_LAT = ~DEBUG1_LAT
#define DEBUG1_GetValue() DEBUG1_LAT

//DEBUG0 Output - RA0
#define DEBUG0_LAT LATA0
#define DEBUG0_TRIS TRISA0
#define DEBUG0_ANSEL ANSELA0
#define DEBUG0_SetHigh() DEBUG0_LAT = 1
#define DEBUG0_SetLow() DEBUG0_LAT = 0
#define DEBUG0_Toggle() DEBUG0_LAT = ~DEBUG0_LAT
#define DEBUG0_GetValue() DEBUG0_LAT
    
//Pump Priming SW - RB5
#define PRIME_SW_LAT LATB5
#define PRIME_SW_TRIS TRISB5
#define PRIME_SW_ANSEL ANSELB5
#define PRIME_SW_WPU WPUB5
#define PRIME_SW_CLC_IN 0b001101
#define DEBUG0_GetValue() DEBUG0_LAT
    
//I2C Address I/O
    
//ADDR1 - RB4
#define ADDR1_TRIS TRISB4
#define ADDR1_ANSEL ANSELB4
#define ADDR0_WPU WPUB4
#define ADDR1_GetValue() PORTBbits.RB4
    
//ADDR0 - RC0
#define ADDR0_TRIS TRISC0
#define ADDR0_ANSEL ANSELC0
#define ADDR1_WPU WPUC0
#define ADDR0_GetValue() PORTCbits.RC0
    
#ifdef	__cplusplus
}
#endif

#endif	/* GPIO_MACROS_H */

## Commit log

2023-06-14 Improvements to schematic
    [Control Board.kicad_pcb, Control Board.kicad_sch]
2023-06-16 Work on Schematic + README
    [Control Board.kicad_sch]
2023-06-19 Started PCB layout
    [Control Board.kicad_pcb, Control Board.kicad_sch]
2023-06-27 More changes to PCB / Schematic
    Schematic complete, PCB in progress
    [Control Board.kicad_pcb, Control Board.kicad_sch]
2023-06-29 More work on PCB
    [Control Board.kicad_pcb, Control Board.kicad_sch]
2023-06-29 Draft of PCB
    [Control Board.kicad_pcb, Control Board.kicad_sch]
2023-06-29 Finished PCB
    [Control Board.kicad_pcb, Control Board.kicad_sch]
2023-07-07 Firmware Tweaks, Schematic Notations
    Began to implement SW Registers. Adjusted part annotations / DNP status (no layout changes)
    [Control Board.kicad_sch, Control Board.xlsx]
2023-07-10 PWM / NCO Code
2023-07-18 Bug fixes. Added VSS input
    [ADCC.c, ADCC.h, GPIO.c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]
2023-07-18 Bug fixes. Added test script for MCP2221A
    [MCP2221A Script.csv]
2023-07-18 Improved I2C Error Handling
    [i2c_client.c]
2023-07-21 Added DAC2 for Self-Testing. Updated PCB/SCH to Rev A2
    Increased size of pads for reset switch. Added debug header for OPAMP. Added pin 1 marker for programming.
    [Control Board.kicad_pcb, Control Board.kicad_sch, MCP2221A Script.csv]
2023-07-21 PCB fixes
    [Control Board.kicad_pcb]
2023-07-25 Initial Commit of Python Library
    Includes bug fix for Pump
    [system.c]
2024-03-21 Changed default PWM DC
2025-05-19 Added 3d models
    [cameraBox.FCStd, cameraBox.step, flagMount.FCStd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]
